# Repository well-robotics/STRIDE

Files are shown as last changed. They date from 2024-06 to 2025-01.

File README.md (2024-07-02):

# Open-Source Planar Biped Robot STRIDE
Hardware STRIDE
Simulated STRIDE
## Introduction
STRIDE is a low cost, easy-to-build yet versatile and robust planar bipedal robot platform for both educational and research purposes. The robot walks in a circular path constrained by a boom with a four-bar linkage. Except the basic robot and boom designs, a modular rough terrain setup and a quatitative measurable disturbance injection system are presented for system and algorithms validation purposes. The terrain setup can be easily reconfigured to fulfill different research purposes while the disturbance injection system built with propellors provide measurable yet decoupled disturbances to test adaptation algorithms.  
This repo includes the software and hardware design of a open-sourced planar biped robot STRIDE and a step-to-step guid on how to make mechanical assemblies and how to implement a walking controller.
## Repository Structure
The package mainly consists of two folders, one for mechanical designs and one for software. The BOM includes all the materials needed to build the robot, along with an estimated cost for each item.
## Installation
### ROS2 
This project uses ROS2 as communication middleware. To configure ROS2 on workstation or PC, we recommend using Ubuntu 22.04 and ROS2 Humble which is validated by us. \
The installation guideline of ROS2 Humble is in: https://docs.ros.org/en/humble/Installation/Ubuntu-Install-Debians.html. To configure ROS2 on Raspberry Pi 4b+, you should build from source, follow the guidelines in https://docs.ros.org/en/humble/How-To-Guides/Installing-on-Raspberry-Pi.html and https://docs.ros.org/en/humble/Installation/Alternatives/Ubuntu-Development-Setup.html. \
After installation, you can verify the setup by checking environment variables: 
```bash
  printenv | grep -i ROS
```
Once ROS2 is setup successsfully, you should first build a ROS2 workspace
```bash
mkdir -p ~/ros2_ws/src
cd ~/ros2_ws
colcon build
```
Then clone the folder
```bash
git clone https://github.com/well-robotics/STRIDE.git
```
### LibSerial
This project uses LibSerial as the serial communication middleware, the detailed installation can be found in the Github page of LibSerial: https://github.com/crayzeewulf/libserial. Following the guideline of CMake based installations and use default installation folder. 

### FROST
FROST is used to generate dynamic libraries for the project. To install FROST on Windows, follow the guidelines in https://ayonga.github.io/frost-dev/pages/installation.html. Several things should be noticed: 
1. The version of Mathematica should be equal or lower than 12.3
2. Remember to change the Mathematica version in mathrun.m
### qpOASES
qpOASES is used to solve formulated QP problems when solving for desired joint torques. To install qpOASES on Windows, follow https://github.com/coin-or/qpOASES for guidelines. Several things should be noticed: 
1. The Matlab interface should be recompiled using Visual Studio 

## Launch Example
Once all the dependencies are well configured, first build the whole package: 
```bash
cd ~/ros2_ws
colcon build
```
Then, you can run the commands below to launch simulation and hardware nodes
### MuJoco Simulation
To run the MuJoco simulation, run
```bash
ros2 launch mujoco simulation_launch.py
```
Then a MuJoco simulation window will show up and the robot will be hang in the air initially. 
### Hardware Nodes
To run hardware nodes, run 
```bash
ros2 launch hardware hardware_launch.py
```
This launch file will successfully launch all the nodes when the Arduino Mega, two IMUs and two contact switches are connected to the Raspberry Pi.

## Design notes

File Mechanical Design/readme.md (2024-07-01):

# Mechanical Design
This folder contains the mechanical design of the platform. The structure of the folder is as follow: 
1. **bipedal robot**: this folder contains the mechanical design of the robot
2. **boom**: this folder contains the mechanical design of the base and the boom
3. **hardware**: this folder contains the screws and nuts used during design
4. **rough terrain**: this folder contains the design of the modular rough terrain
A mechanical assembly video file is provided for step-to-step guideline on how to assemble the robot.

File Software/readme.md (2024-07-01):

# Software
This folder organizes the scripts used for the robot platform, categorized based on the tools they leverage.
1. **ROS2**: The ROS2 folder contains all ROS2-related scripts used for both on the hardware and the MuJoco simulator.
2. **Arduino**: The Arduino folder contains the Arduino scripts for controlling the brushed DC motors of the robot's joints and the brushless DC motors in the disturbance injection system.
3. **Matlab**: The Matlab folder contains the Matlab scripts used for generating dynamic libraries, a separate S2S dynamics based controller with QP based WBC controller and an event based simulator.

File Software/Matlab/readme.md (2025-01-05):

This folder contains the codes for dynamics library generation through FROST and a standalone implementation of a scripts based simulator, an H-LIP controller and an instantaneous QP task space controller. 

Folders are organized as follow: 
1. **Animator**: contains the animation related utilities
2. **Controller**: contains the instantaneous QP task space controller 
3. **Dynamics Gen**: contains the scripts for kinematics and dynamics functions generations
4. **Expressions**: contains the generated kinematics and dynamics functions
5. **Main Walking**: contains the utilities relevant to walking

To run the simulator and controller, simply run the script named mainWalking under Main Walking folder.

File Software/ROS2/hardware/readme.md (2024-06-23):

# hardware package
This package contains sensor reading and serial communication nodes, and the controller launch file.

## How to Use

To use this package, please use following 

To run any node, use the following command line:

```
# Check the nodes in this package (in your workspace/src folder)
source ../install/setup.bash 
ros2 pkg executables hardware

# run any node to chceck actuators or sensors:
ros2 run hardware contact_pub

# in a new command line, run this to see if the switches are functioning properlly
source ../install/setup.bash 
ros2 topic list
ros2 topic echo /hardware/ContactState
```

To launch the template controller, run the following line(make sure you have hardware setup and powered properly): 

```
ros2 launch hardware planar_bipedal_hardware_launch.py
```

## Package Structure

The following nodes are included in this package:

1. contact_sensor_node: for contact sensor reading
2. imu_node: for reading pelvis angle and angular velocity
3. roll_velocity_node: for reading x-direction velocity
4. serial_communication_joint_node: for serial communication with Arduino

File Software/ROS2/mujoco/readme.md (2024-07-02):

# Mujoco Package

This package is modified from the [open sourced ROS2 MuJoCo package](https://github.com/MindSpaceInc/Spot-MuJoCo-ROS2) from mindspace.inc.

It creates a simulation thread in MuJoCo with MJCF model file provided by description package. And established a node to send multiple sensor messages to ROS2.

## Package Structure

`MujocoMessageHandler.cpp` is the connection between MuJoCo and ROS2, it samples the required sensor data and publishes to according topics. This includes `/ContactState`, `/JointState`, `/ImuData`.(Also check communication/msg for details).

simulation executable(main.cc) establishes the physics thread in MuJoCo

## Installation Guide

This guide referenced this [installation instructions][https://gist.github.com/saratrajput/60b1310fe9d9df664f9983b38b50d5da], To download MuJoCo, please go check its [releases][https://github.com/google-deepmind/mujoco/releases]. This version of STRIDE uses [2.3.2][https://github.com/google-deepmind/mujoco/releases/tag/2.3.2]. Take 2.3.2 as an example, after downloading the zip file:

```bash
cd /home/username/
mkdir .mujoco
tar -xvf mujoco232-linux-x86_64.tar.gz -C ~/.mujoco/
```

Add these lines to your `.bashrc`:

```bas
export LD_LIBRARY_PATH=$LD_LIBRARY_PATH:/home/username/.mujoco/mujoco-2.3.2/lib
export LD_LIBRARY_PATH=$LD_LIBRARY_PATH:/usr/lib/nvidia
export PATH="$LD_LIBRARY_PATH:$PATH"
export LD_PRELOAD=/usr/lib/x86_64-linux-gnu/libGLEW.so
```

To test if the installation is successful, use the following line to test:

```bash
cd ~/.mujoco/mujoco210/bin
./simulate ../model/humanoid.xml
```

### Things to notice

1. **The hold-release procedure**: It is realized with [sim_helper](src/Planar-Bipedal-Software-Repo/mujoco/include/mujoco_sim_helper.hpp). It first holds the floating base of the robot by giving a extremely large damping and stiffness, then slowly release it to the ground.
   1. The time variables are set locally.
   2. The fixed degrees of freedom are the ones on the floating base. They will remain a small value after it is released.
2. **Applying control to MuJoCo**: check apply_ctrl() function in main.cc. It realized a PD+feedforward controller of motors in MuJoCo. The data is directly obtained from shared pointer in Message Handler Node.
3. **Launch file**: The simulation-launch file launches simulator and controller simultaneously. The model xml file and the control yaml file are also specified here.

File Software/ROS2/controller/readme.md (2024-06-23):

# Hlip package
This package implements the S2S dynamics based controller for STRIDE
## package structure
This package contains three layers of abstraction: 
1. HLIP class captures the essence of reduced-order HLIP model which plans the desired step size with reference step size
2. output_controller class is used to plan desired joint trajectories for the planar bipedal robot based on desired outputs
3. S2S_controller node takes in desired hardware inputs, instantiates a output_controller class to plan in 200Hz and outputs the desired joint positions and velocitites

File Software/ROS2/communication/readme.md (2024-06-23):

# Communication package
This package contains all the self-defined message and service interfaces being used in simulation and hardware.
## hardware interfaces  
1. ActuatorCmds.msg: for sending desired joint trajectories from Raspberry Pi to Arduino
2. ContactState.msg: for sending contact sensor states from contact sensor node to walking controller
3. JointStates.msg: for sending joint encoder readings from serial communication node to walking controller 
4. PitchState.msg: for sending pelvis angle and pelvis angular velocity to walking controller
4. MotionCommands.msg: for outputs states logging

## simulation interfaces
1. MotionCommands.msg: for outputs states logging
2. SimulationReset.srv: for MuJoco simulation reset

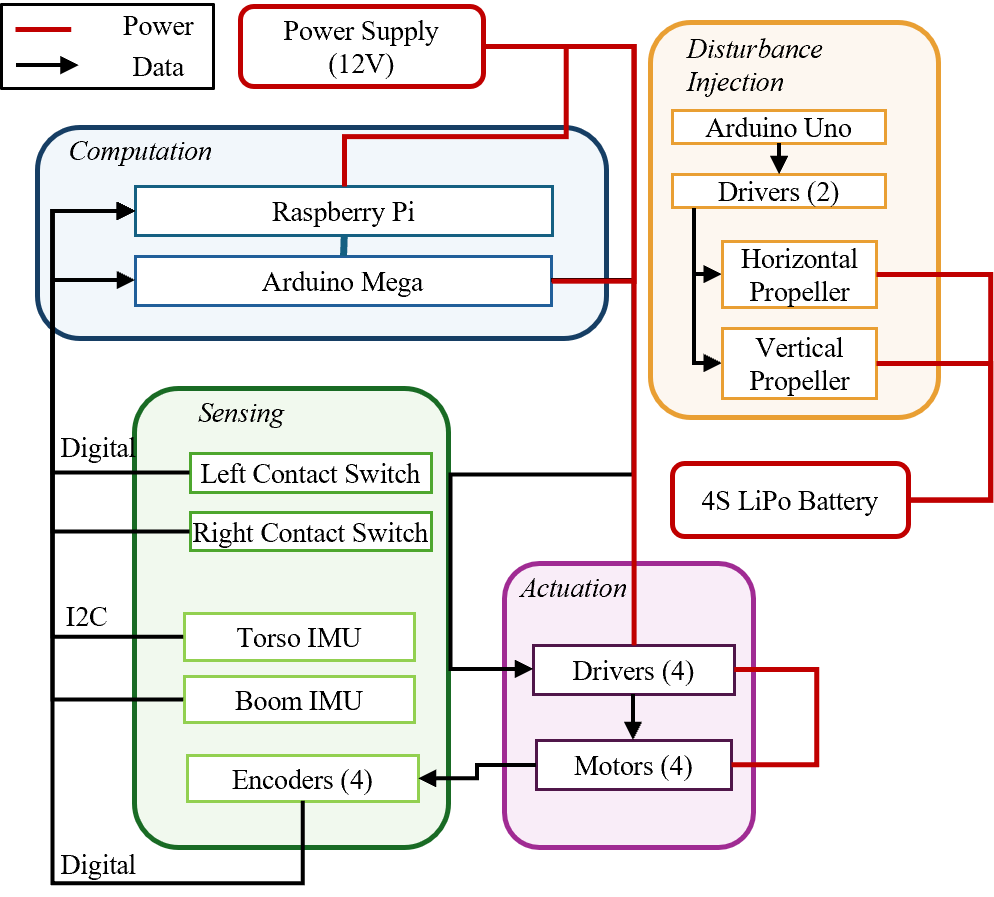
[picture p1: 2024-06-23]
electronics_diagram.png

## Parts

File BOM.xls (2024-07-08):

Mechanical parts | numbers | prices (with educational discount) | source
1140-0006-0144 | 1 | 12.74 | https://www.gobilda.com/
2800-0004-0010 | 249 | 28.8
2802-0004-0008 | 60 | 8.13
4103-0032-0312 | 1 | 7.98
1109-0024-0528 | 8 | 89.68
1139-0024-0056 | 4 | 5.94
1201-0043-0002 | 18 | 106.92
1120-0004-0120 | 3 | 17.82
1401-0043-0032 | 15 | 101.85
2800-0004-0014 | 27 | 3.14
1126-0001-0001 | 8 | 8.48
2805-0004-0108 | 16 | 8.49
2800-0004-0006 | 46 | 5.08
1204-0001-0002 | 8 | 16.96
1604-0043-0032 | 4 | 44.16
1502-0006-0020 | 4 | 1.48
1502-0006-0030 | 4 | 1.52
2803-0039-0007 | 6 | 7.62
1400-0032-0032 | 8 | 54.32
2800-0004-0012 | 12 | 3.59
4103-0032-0043 | 4 | 13.56
1506-0032-0004 | 16 | 20.32
1121-0007-0192 | 2 | 15.28
1120-0003-0096 | 2 | 10.18
1123-0043-0096 | 1 | 2.97
1201-0024-0001 | 2 | 11.88
1106-0005-0040 | 8 | 18.96
1123-0043-0144 | 2 | 7.64
1120-0001-0048 | 1 | 3.39
2800-0004-0018 | 13 | 3.31
2803-0007-0007 | 33 | 8.48
2800-0004-0030 | 4 | 3.65
1123-0043-0144 | 2 | 7.64
4103-0032-0432 | 1 | 10.02
4103-0032-0048 | 4 | 13.92
1502-0006-0010 | 2 | 1.39
2802-0004-0016 | 2 | 3.22
4103-0032-1200 | 2 | 46.06
1604-0043-0032 | 8 | 88.32
1111-0004-0001 | 2 | 11.88
1123-0043-0144 | 4 | 15.28
1116-0040-0088 | 2 | 4.74
5204-8002-0019 | 2 | 76.48
5202-2402-0019 | 2 | 76.48
1112-0001-0048 | 2 | 5.08
1611-0514-4008 | 11 | 30.54
1108-0001-0001 | 4 | 6.76
2315-1006-0030 | 2 | 25.48
1504-0032-0025 | 2 | 4.24
1108-0001-0002 | 4 | 8.48
1309-0016-4008 | 6 | 40.74
1611-0514-0006 | 2 | 3.39
1400-0032-0014 | 4 | 23.76
4100-1214-0200 | 2 | 7.64
1200-0032-0001 | 4 | 20.36
1102-0009-0072 | 4 | 5.26
1516-4008-0800 | 2 | 6.37
2315-4008-0030 | 2 | 25.48
1113-0001-0048 | 4 | 10.16
 |  |  | source: https://www.mcmaster.com/
91290A119 | 8 | 14.38
90591A121 | 8 | 1.9
98035A102 | 4 | 14.66
Electronic Parts
Arduino Uno | 1 | 17 | https://www.amazon.com/ELEGOO-Board-ATmega328P-ATMEGA16U2-Compliant/dp/B01EWOE0UU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
Arduino Mega | 1 | 20 | https://www.amazon.com/ELEGOO-Compatible-Arduino-Projects-Compliant/dp/B01H4ZLZLQ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
Raspberry Pi 4b+ | 1 | 62 | https://www.amazon.com/Raspberry-Model-2019-Quad-Bluetooth/dp/B07TC2BK1X
Pololu VNH5019 | 4 | 119.8 | https://www.pololu.com/product/1451
Gemfan Propeller 51466 | 2 | 9 | https://www.getfpv.com/gemfan-hurricane-51466-propeller-set-of-4.html
T-Motor V2207 | 2 | 27.8 | https://store.tmotor.com/product/v2207-v2-fpv-motor.html
Weight 5lb | 3 | 15 | https://www.amazon.com/Cap-2-Inch-Olympic-Weight-OPHWIS-005/dp/B09NLD1NP9?sp_csd=d2lkZ2V0TmFtZT1zcF9hdGY
SparkFun ICM20948 | 2 | 37 | https://www.sparkfun.com/products/15335
Contact Switch | 2 | 9.99 | https://www.amazon.com/gp/product/B09SLHQVHL/ref=ox_sc_saved_image_3?smid=A1POY47GM797OI&psc=1
VOYEE Xbox360 Joy Stick | 1 | 16.99 | https://www.amazon.com/VOYEE-Controller-Compatible-Microsoft-Windows/dp/B07WD4TSNQ
AC DC converter | 1 | 26.99 | https://www.amazon.com/EXENWING-12V-Universal-Converter-Transformer/dp/B0CHS2JDV8
3D printed Parts
Terrain pieces | 20 | 80.4
Footpad | 2 | 0.46
Electronics Hull | 1 | 2.2
Terrain Components
Pebble Stones |  | 25.92 | https://www.amazon.com/gp/product/B0B1T4XZRJ/ref=ox_sc_saved_image_2?smid=A1RBNAZ9ARM7RC&psc=1
Clay Pebbles |  | 15.99 | https://www.amazon.com/gp/product/B0C7CGPT5L/ref=ox_sc_saved_image_3?smid=A1NTNJ5WND4GE5&th=1
Chickpeas |  | 18.95 | https://www.amazon.com/gp/product/B001PEWJWC/ref=ox_sc_saved_image_2?smid=A74292C1GAH2Y&psc=1
Poppy Seeds |  | 5.35 | https://www.sfherb.com/Poppy-Seeds--1-Lb_p_80.html
 |  | 1775.27

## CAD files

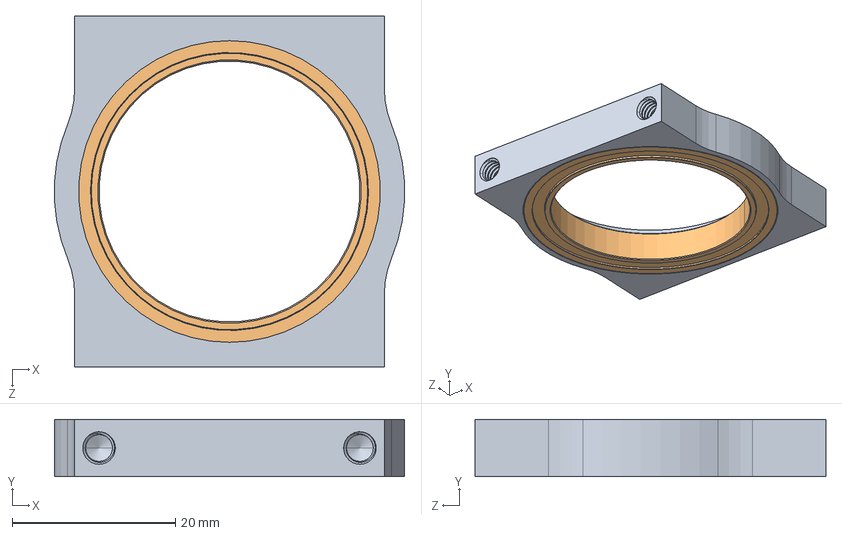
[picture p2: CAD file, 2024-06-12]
Mechanical Design/bipedal robot/robot base/1604-0043-0032 assembly.SLDASM
42.9 x 7.00 x 43.0 mm
1604-0043-0032.STEP
1601-0039-00032.STEP

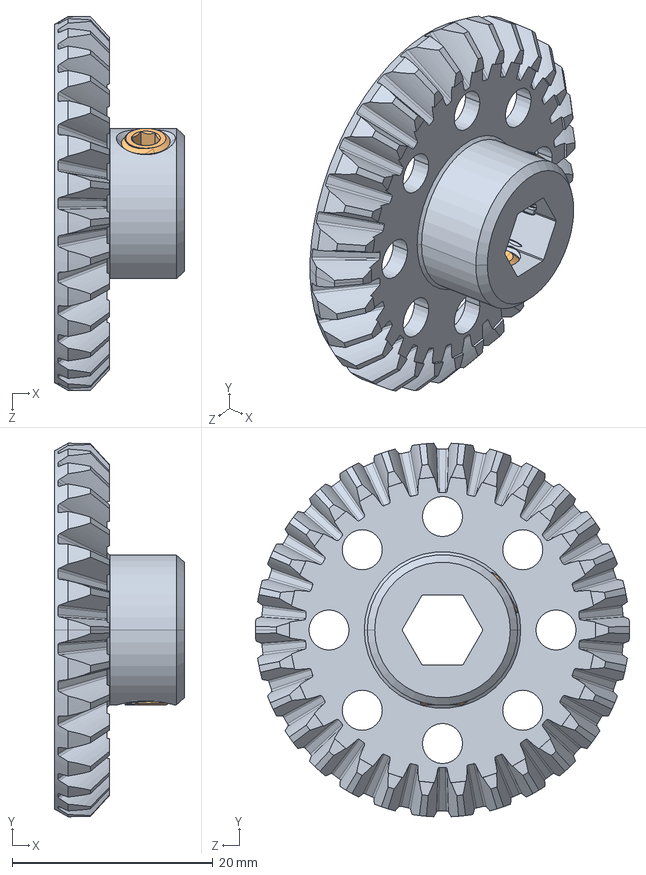
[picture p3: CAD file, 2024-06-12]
Mechanical Design/bipedal robot/robot leg knee/2315-4008-0030 assembly.SLDASM
13.0 x 37.2 x 37.3 mm
2315-4008-0030.STEP
2806-0005-0004_91390A117.STEP x 2

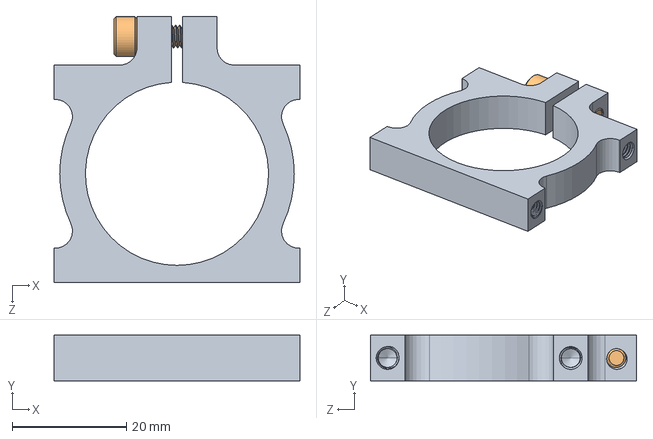
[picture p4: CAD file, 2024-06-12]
Mechanical Design/boom/bar/1401-0043-0032 assembly.SLDASM
43.0 x 8.00 x 46.5 mm
1401-0043-0032.STEP
2800-0004-0014_90128A207.STEP

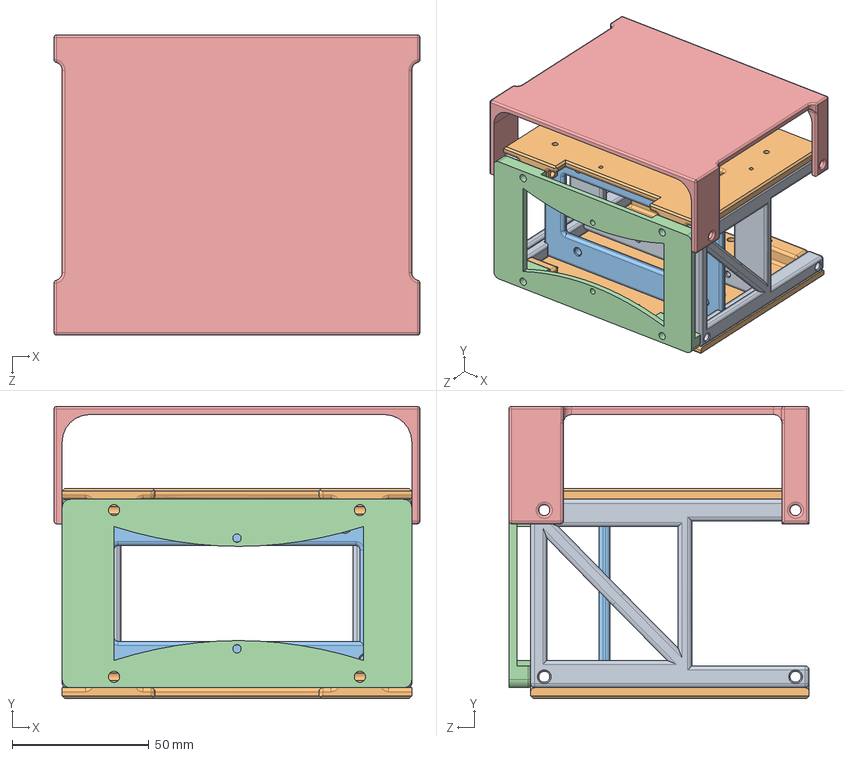
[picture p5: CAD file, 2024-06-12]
Mechanical Design/bipedal robot/Elelctronics_mounting/ElecMount.SLDASM
134.0 x 107.0 x 110.0 mm
mounting_base
shield x 2
Arduino_New
upper_energy_board
Wire_shading_part

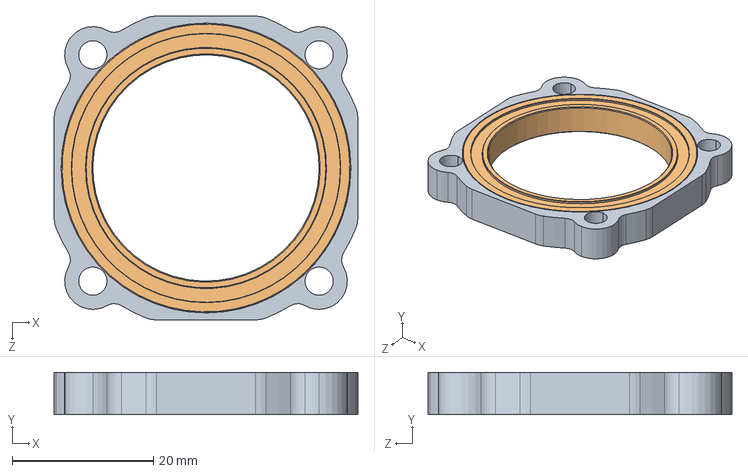
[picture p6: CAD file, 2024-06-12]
Mechanical Design/boom/bar/joint bar/1603-0032-0032 assembly.SLDASM
43.0 x 6.00 x 43.0 mm
1603-0032-0032.STEP
1601-0039-00032.STEP

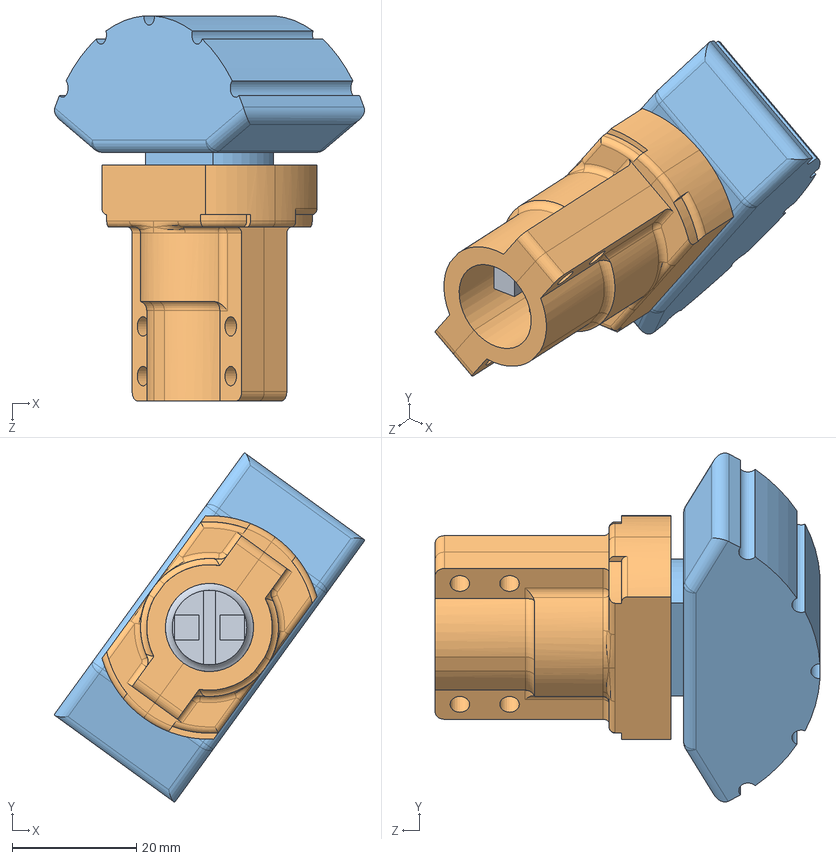
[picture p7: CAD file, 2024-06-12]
Mechanical Design/bipedal robot/contact switch/contact_TPU_footpad.SLDASM
49.9 x 56.2 x 62.0 mm
touch_sensor_bare
contact_switch_mount_half_TPU_footpad x 2
flat_foot_sticker

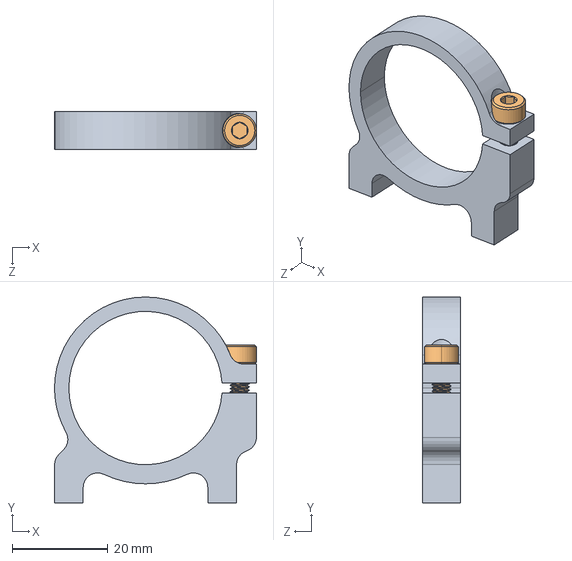
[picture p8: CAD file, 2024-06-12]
Mechanical Design/boom/base/support/1400-0032-0032 assembly.SLDASM
42.2 x 43.0 x 8.00 mm
1400-0032-0032.STEP
2800-0004-0012_90128A207.STEP

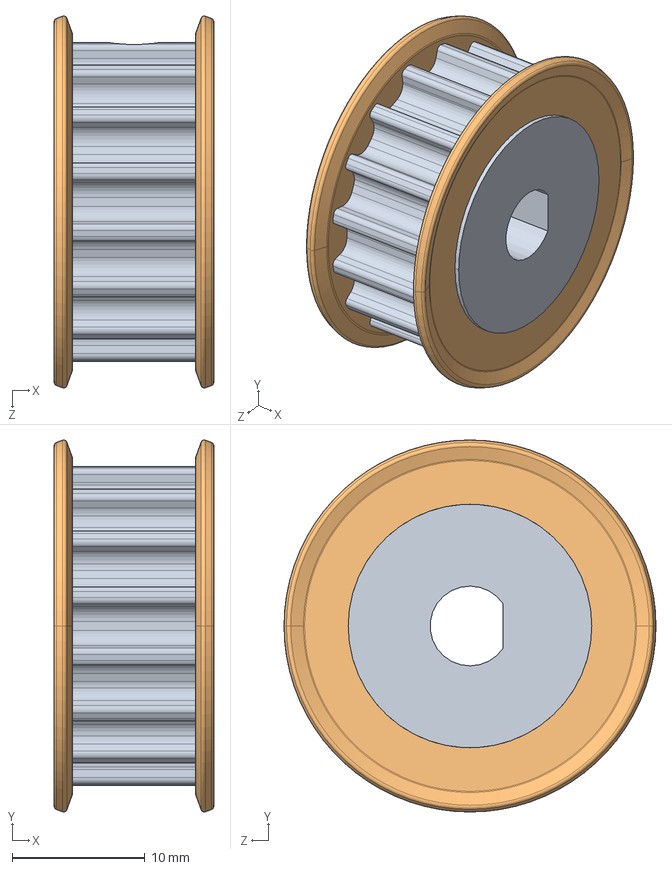
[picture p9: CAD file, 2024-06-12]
Mechanical Design/bipedal robot/3414-1006-0016 assembly.SLDASM
12.0 x 28.0 x 28.0 mm
3414-1006-0016 body.STEP
3414-4008-0016 ring.STEP x 2
2806-0005-0006_91390A118.STEP

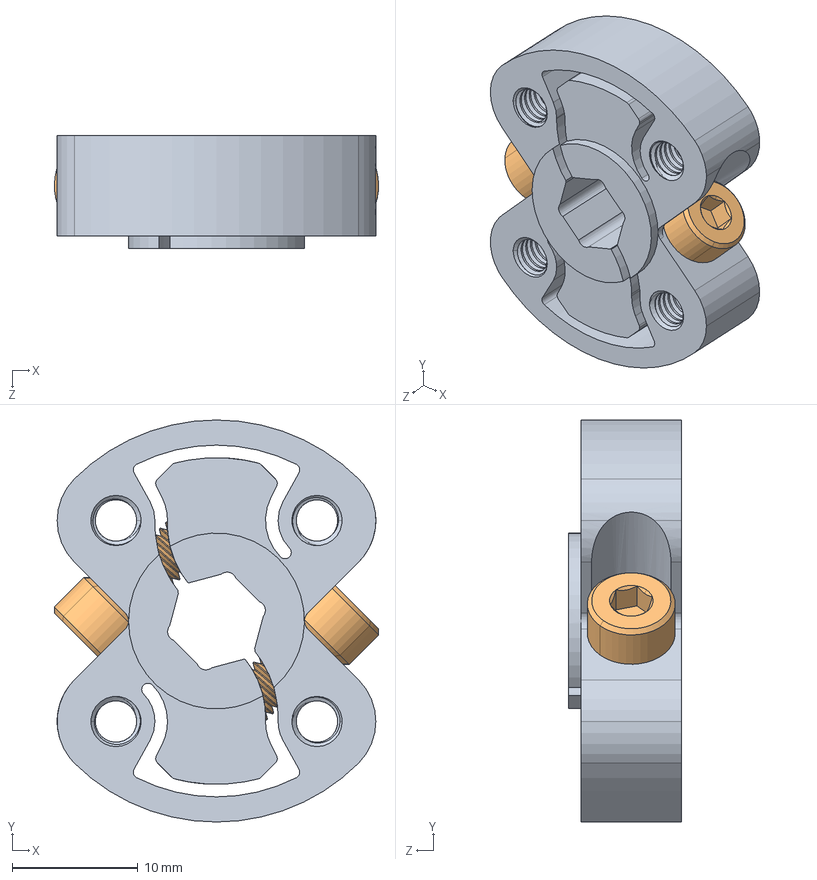
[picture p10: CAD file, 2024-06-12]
Mechanical Design/bipedal robot/robot leg knee/1309-0016-4008 assembly.SLDASM
25.8 x 32.0 x 9.00 mm
1309-0016-4008.STEP
2800-0004-0014_90128A207.STEP x 2

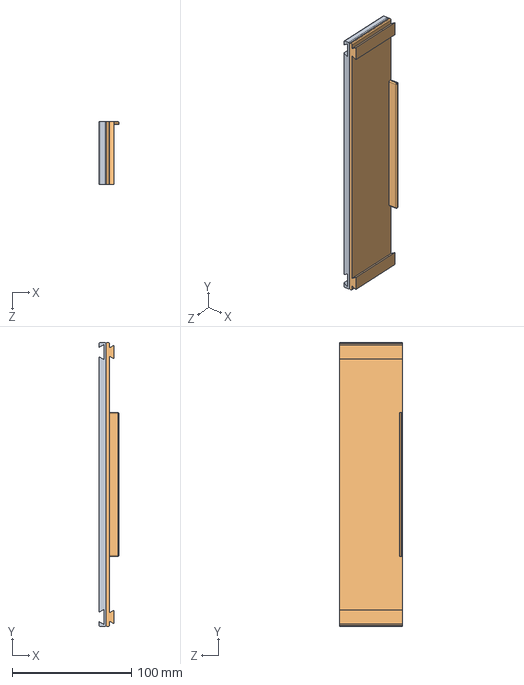
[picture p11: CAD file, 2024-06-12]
Mechanical Design/rough_terrain/middle part.SLDASM
16.8 x 238.0 x 53.0 mm
side_part_female
side_part_male

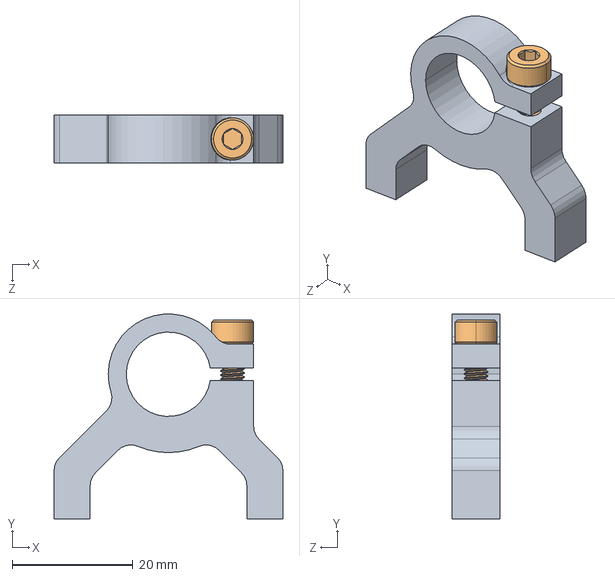
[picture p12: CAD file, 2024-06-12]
Mechanical Design/bipedal robot/robot leg knee/1400-0032-0014 assembly.SLDASM
38.0 x 34.0 x 8.00 mm
1400-0032-0014.STEP
2800-0004-0012_90128A207.STEP

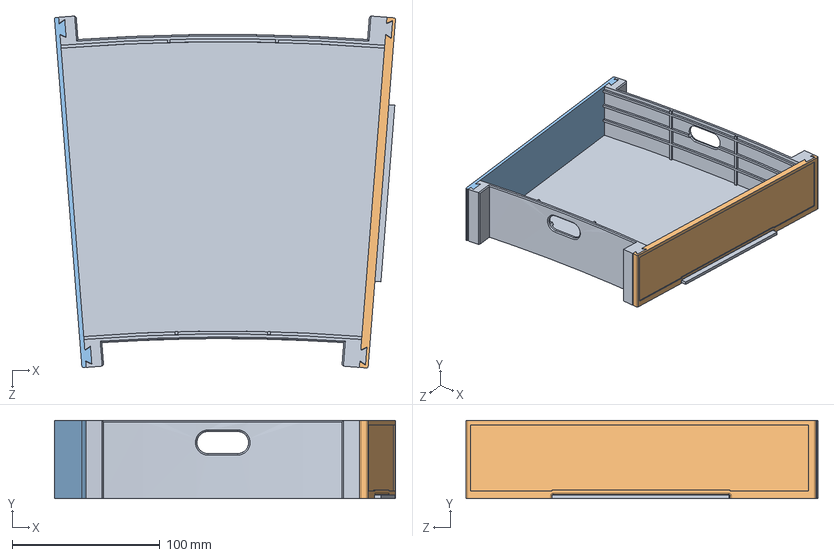
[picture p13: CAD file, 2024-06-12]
Mechanical Design/rough_terrain/side_parts_assemb.SLDASM
231.1 x 53.0 x 238.5 mm
new_terrain_piece
side_part_female
side_part_male

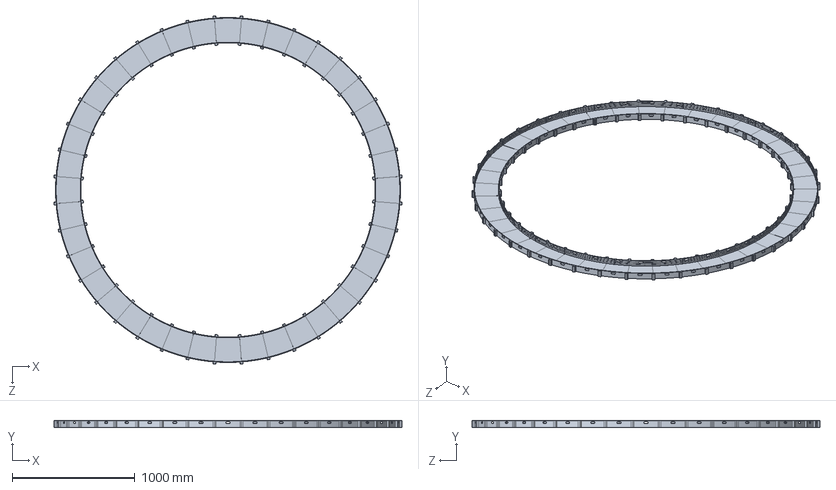
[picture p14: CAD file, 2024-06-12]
Mechanical Design/rough_terrain/terrainAssembly.SLDASM
2831.0 x 53.0 x 2831.0 mm
new_terrain_piece x 40

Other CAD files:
Mechanical Design/bipedal robot/2315-1006-0030 assembly.SLDASM
Mechanical Design/boom/bar/1604-0043-0032 assembly.SLDASM
Mechanical Design/bipedal robot/robot base/1401-0043-0032 assembly.SLDASM
Mechanical Design/boom/base/support base/1401-0043-0032 assembly.SLDASM
Mechanical Design/bipedal robot/1112-0001-0048.SLDPRT
Mechanical Design/bipedal robot/1611-0514-4008.SLDPRT
Mechanical Design/bipedal robot/3D printed parts/IMU_board.SLDPRT
Mechanical Design/bipedal robot/3D printed parts/gear_standoff_horizontal.SLDPRT
Mechanical Design/bipedal robot/3D printed parts/gear_standoff_vertical.SLDPRT
Mechanical Design/bipedal robot/Elelctronics_mounting/Arduino_New.SLDPRT
Mechanical Design/bipedal robot/Elelctronics_mounting/Wire_shading_part.SLDPRT
Mechanical Design/bipedal robot/Elelctronics_mounting/electric_mounting_cover.SLDPRT
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

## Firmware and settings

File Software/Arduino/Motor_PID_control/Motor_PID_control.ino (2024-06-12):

//// This code is about reading the encoder data using interrupts then calculate the PID values and put the PID data into the motors
#include <stdint.h> 
// serial communication variables
int motor_id[4] = {0,1,2,3}; 
const char numChars = 20;
uint8_t receiveddata[numChars];
uint8_t joint_real_encoded[8];
// double joint_states_desired[4] = {0.00,0.00,0.00,0.00};
double joint_states_desired[8] = {0.00,0.00,0.00,0.00,0.00,0.00,0.00,0.00}; 
double joint_real[4] = {0.000,0.000,0.000,0.000};

int debug_bit = 0;

// PWM pins
int PWM_pin[4] {7, 8, 11,12};  // 8 7 12 11 
int PWM_pin_cw[4] = {28,31,33,34}; 
int PWM_pin_ccw[4] = {29,30,32,35};
// PWM variables
double actual[4]; 
int direct[4] = {1,1,1,1}; 
double pwm_grav[4] = {0.0,0.0,0.0,0.0};


// Encoder pins
int encoder_pin_cw[4] = {2,18,20,21};
int encoder_pin_ccw[4] = {3,19,14,15}; 
// filter for encoders
class MovingAverageFilter{
public:  
  int window_size; 
  double previous_data[50] = {0}; // the max size of the window is set to 50
  MovingAverageFilter(int size){
    this->window_size = size; 
  } 
  double calc(){
    double output =0; 
    for(int i=0;i<window_size;i++){
      output = output + previous_data[i]; 
    }
    return (output/window_size); 
  }
  void renew(double input){
    for(int i=0;i<window_size;i++){
      previous_data[i]= previous_data[i+1]; 
    }
    previous_data[window_size - 1] = input; 
  }
};
MovingAverageFilter filter[4](2);
// encoder and position readings 
double resolution = 1992.3/(4*2*3.14159);
int count[4] = {0,0,0,0}; 
double position[4] = {0,0,0,0}; 

unsigned long start_time = millis(); 
int count_time_debug = 0; 
class PID{
public:  
  PID(double kp,double kd,double ki):Kp(kp),Kd(kd),Ki(ki){}; 
  double ComputeOutput(){
    // this function will compute the output to the PWM write function
    unsigned long now = millis(); 
    double timeChange = (double)((now - lastTime)); 
    // compute errors
    double error = this->setpoint - this->input; 
    ErrorSum += (error*timeChange); 
    double dErr = (error - lastError) / timeChange; 
    output = Kp*error + Ki*ErrorSum+ Kd*dErr;
    if (output>100){
      output = 100;
    }
    else if (output<-100){
      output = -100; 
    }
    lastError = error; 
    lastTime = now;
    return output;  
  }
  void Setsetpoint(double in){
    this-> setpoint = in;
  }
  void SetRealPosition(double pos){
    this-> input = pos; 
  }
private:   
  double Kp; 
  double Kd; 
  double Ki;  
  double ErrorSum = 0; 
  double lastError; 
  unsigned long lastTime = 0;
  double input = 0; 
  double output = 0;
  double setpoint = 0;   
};
// build up PID controllers
PID pd_controller[4]={PID(100.0,10.0,0),PID(100.0,10.0,0),PID(100.0,10.0,0),PID(100.0,10.0,0)};
void getPosition(){
  int i = 0; 
  for(i=0;i<4;i++){
    joint_real[i] = count[i]/resolution;
    filter[i].renew(joint_real[i]); 
    joint_real[i] = filter[i].calc();
  }  
}
void checkBound(){
  int i = 0;
  for(i=0;i<4;i++){
    if(i == 1 || i == 3){
    if(joint_states_desired[i] > 2.2 ){
      joint_states_desired[i] = 2.2; 
    }
    else if(joint_states_desired[i] < -1.7){
      joint_states_desired[i] = -1.7;
    }
    }
    if(i == 0 || i == 2){
    if(joint_states_desired[i] > 1.7 ){
      joint_states_desired[i] = 1.7; 
    }
    else if(joint_states_desired[i] < -1.7){
      joint_states_desired[i] = -1.7;
    }
    }

  }
}

void setup()
{
  Serial.begin(115200);
  // setup a high PWM frequency
  TCCR1A = 0b10100000;
  TCCR1B = 0b00010001;
  TCCR4A = 0b10100000;
  TCCR4B = 0b00010001;
  ICR1 = 100;
  ICR4 = 100;
  int i;
  for (i=0;i<4;i++){
    // set the encoder pin mode as input 
    pinMode(encoder_pin_cw[i],INPUT_PULLUP);
    pinMode(encoder_pin_ccw[i],INPUT_PULLUP);
    // set the PWM pin mode as output
    pinMode(PWM_pin[i],OUTPUT);
    pinMode(PWM_pin_cw[i],OUTPUT);
    pinMode(PWM_pin_ccw[i],OUTPUT);

  }
  // attach intterupt for encoder pins 
  attachInterrupt(digitalPinToInterrupt(encoder_pin_cw[0]),readEncoder<0>,RISING);
  attachInterrupt(digitalPinToInterrupt(encoder_pin_cw[1]),readEncoder<1>,RISING);
  attachInterrupt(digitalPinToInterrupt(encoder_pin_cw[2]),readEncoder<2>,RISING);
  attachInterrupt(digitalPinToInterrupt(encoder_pin_cw[3]),readEncoder<3>,RISING);
}
template<int j>
void readEncoder(){
/////////////////// method reading two pins /////////////////
  // old_val[j] = new_val[j]; 
  // new_val[j] = digitalRead(encoder_pin_cw[j])*2 + digitalRead(encoder_pin_ccw[j]);
  // out = QEM[old_val[j]*4+new_val[j]]; 
  // count[j] = count[j] + out; 

///////////////// method only read one pin  ///////////////
  int b = digitalRead(encoder_pin_ccw[j]);
  if(b>0){
    count[j]--; // ++ for pull down
  }
  else{
    count[j]++; 
  }
}

void getPosValue_byte(){
    static boolean recvInProgress = false;
    static byte ndx = 0;
    char startMarker = 's'; 
    char endMarker = 'e';
    char rc;
    while (Serial.available() > 0) { 
        rc = Serial.read();
        debug_bit = 1; 
        if (recvInProgress == true) {
            if (rc != endMarker) {
                receiveddata[ndx] = rc;
                ndx++;
                if (ndx >= numChars) {
                    ndx = numChars - 1;
                }
            }
            else {
                recvInProgress = false;
                ndx = 0;
            }
        }         
        if (rc == startMarker) {
            recvInProgress = true;
        }
    }
}

void PWMWrite(int motor_id, double DutyCycle, int direc){
  if (direc == 1){
    digitalWrite(PWM_pin_ccw[motor_id],LOW);
    digitalWrite(PWM_pin_cw[motor_id],HIGH); 
  }
  else if (direc == 0){
    digitalWrite(PWM_pin_cw[motor_id],LOW);
    digitalWrite(PWM_pin_ccw[motor_id],HIGH); 
  }
  double OutPutValue = DutyCycle*255/100;
  analogWrite(PWM_pin[motor_id],int(OutPutValue));
}

void receivedDataDecode(){
  int i;
  uint8_t j1[2];
  uint8_t j2[2];
  uint8_t j3[2];
  uint8_t j4[2];
  uint8_t j5[2];
  uint8_t j6[2];
  uint8_t j7[2];
  uint8_t j8[2];
  
  for (i = 0; i < 2; i++) {
    j1[i] = receiveddata[i];
    j2[i] = receiveddata[i + 2];
    j3[i] = receiveddata[i + 4];
    j4[i] = receiveddata[i + 6];
    j5[i] = receiveddata[i + 8];
    j6[i] = receiveddata[i + 10];
    j7[i] = receiveddata[i + 12];
    j8[i] = receiveddata[i + 14];
  }

  int16_t temp[8];
  temp[0] = (j1[0] << 8) | j1[1];
  temp[1] = (j2[0] << 8) | j2[1];
  temp[2] = (j3[0] << 8) | j3[1];
  temp[3] = (j4[0] << 8) | j4[1];
  temp[4] = (j5[0] << 8) | j5[1];
  temp[5] = (j6[0] << 8) | j6[1];
  temp[6] = (j7[0] << 8) | j7[1];
  temp[7] = (j8[0] << 8) | j8[1];

  joint_states_desired[0] = temp[0] / 100.0;
  joint_states_desired[1] = temp[1] / 100.0;
  joint_states_desired[2] = temp[2] / 100.0;
  joint_states_desired[3] = temp[3] / 100.0;
  joint_states_desired[4] = temp[4] / 100.0;
  joint_states_desired[5] = temp[5] / 100.0;
  joint_states_desired[6] = temp[6] / 100.0;
  joint_states_desired[7] = temp[7] / 100.0; 
}

void torquePWMMap(){
  // this method maps torque compensation values to PWM values using: v_pwm = R/(KT*N)*tau
  // motor params: N = 71.2, R = 1.3043, KT = 0.014
  double temp[4] = {0.0,0.0,0.0,0.0};
  int i; 
  for(i=0;i<4;i++){
    temp[i] = 1.3043/(0.014*71.2)*joint_states_desired[i+4];
    pwm_grav[i] = map(temp[i],-12.0,12.0,-100.0,100.0); 
  }
}

void sendingDataEncode() {
  // this method encode the subscribed data from double to char
  int i;
  int16_t temp[4];
  for (i = 0; i < 4; i++) {
    temp[i] = (int16_t)(float_round(joint_real[i]) * 100);  // round to two digits, times 100 and type cast to int8_t
  }
  for (i = 0; i < 4; i++) {
    joint_real_encoded[i * 2 + 1] = temp[i] & 0x00ff;   // get the byte in 0x0b
    joint_real_encoded[i * 2] = (temp[i] >> 8) & 0xff;  // get the byte in 0xb0
                                                           // cout<<hex<<(unsigned char)joint_desired_encoded[i*2]<<endl;
  }
}

float float_round(double var) {
  // this function rounds a floating point number to two decimal accuracies
  float value = (int)(var * 100);
  return (float)value / 100;
}

long int prev_val;
double generate_sine_wave_debug(){
  // step input
  // return 3.14; // rotate 180 degree
  
  // sine wave
  double period = 0.01;
  unsigned long t = millis();  
  return 3*sin((t-start_time)/period*6.28318);

  // square wave
  // if(t-start_time > 1000){
  //   if(prev_val == 0){
  //     prev_val = 3;
  //     return 3;
  //   }
  //   else{
  //     prev_val = 0;
  //     return 0;
  //   }
  //   start_time = t; 
  // }

}

void loop(){  
  // generate a sine wave for testing
  //double trajectory_debug = generate_sine_wave_debug(); 

  // read desired trajectory from Raspberry Pi 
  getPosValue_byte(); 
  receivedDataDecode();
  debug_bit == 0;
  getPosition(); 
  // send the real joint values
  sendingDataEncode();
  int i;
  Serial.write('s');
  for(i=0;i<8;i++){
    Serial.write(joint_real_encoded[i]);
  }
  Serial.write('e');

  // do PD control for motors 
  checkBound();
  for(i=0;i<4;i++){
    pd_controller[i].Setsetpoint(joint_states_desired[i]); 
    pd_controller[i].SetRealPosition(joint_real[i]);
    torquePWMMap();
    double PWM = pd_controller[i].ComputeOutput()+pwm_grav[i]; 
    if(PWM < 0){
      PWM = -PWM; 
      direct[i] = 0; 
    }
    else{
      direct[i] = 1; 
    }
    PWMWrite(i,PWM,direct[i]); 
 }
  long int b = micros();
}

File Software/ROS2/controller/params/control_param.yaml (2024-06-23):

# sim_controller:
#   ros__parameters:
#     # kp_hip:  2.   #4. #1.6 #0.8
#     # kp_knee: 1.   #2.5 #1.2 #0.4
#     # kd_hip:  .4   #2.5 #.2
#     # kd_knee: .2  #0.2 #0.12
#     kp_hip:  30.  #25.   #4. #1.6 #0.8
#     kp_knee: 30. #25.   #2.5 #1.2 #0.4
#     kd_hip:  0.2 #0.5   #2.5 #.2
#     kd_knee: 0.2 #0.5 #0.2 #0.12
#     pelvis_init_height: 0.450
#     swing_height: 0.06
#     TSSP: 0.4 # 0.35
#     step_size: 0.1 # 0.2
#     vdes: 0.25
#     COM_height: 0.30 # 0.35

#     com_height_test: 0.30
#     x_swing_test: 0.
#     z_swing_test: 0.0
#     pitch_test: 0.

# tuned using straight knee and straight footpad, Mar 22
S2S_controller:
  ros__parameters:
    kp_hip:  15.
    kp_knee: 15.
    kd_hip:  0.1
    kd_knee: 0.1
    pelvis_init_height: 0.5
    swing_height: 0.06
    TSSP: 0.4
    step_size: 0.08
    vdes: 0.0
    COM_height: 0.34
    # com_height_test: 0.33
    x_swing_test: 0.
    z_swing_test: 0.0
    pitch_test: 0.

sim_hard_bridge:
  ros__parameters:
    kp_hip:  40.
    kp_knee: 40.
    kd_hip:  1.0 #0.6
    kd_knee: 0.6 #0.6
#### before adding gear ratio
    # kp_hip:  50.  
    # kp_knee: 50. 
    # kd_hip:  1. #0.6
    # kd_knee: 1. #0.6

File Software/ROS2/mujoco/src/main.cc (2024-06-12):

//  ros2_mujoco,
// WELL-robotics
// Xiaobin Xiong, modified based on mujoco example and deepbreak example.

#include <chrono>
#include <cstdint>
#include <cstdio>
#include <cstring>
#include <iostream>
#include <memory>
#include <mutex>
#include <new>
#include <string>
#include <thread>
#include <type_traits>
#include <vector>

#include "array_safety.h"
#include "glfw_adapter.h"
#include "simulate.h"
#include <mujoco/mujoco.h>

#include "mujoco_sim_helper.hpp"
#include "MuJoCoMessageHandler.h"
// #include "ros_utilities/ros_utilities.hpp"

#define MUJOCO_PLUGIN_DIR "mujoco_plugin"

extern "C"
{
#include <sys/errno.h>
#include <unistd.h>
}

namespace
{
  namespace mj = ::mujoco;
  namespace mju = ::mujoco::sample_util;

  // constants
  const double syncMisalign =
      0.1; // maximum mis-alignment before re-sync (simulation seconds)
  const double simRefreshFraction =
      0.7;                       // fraction of refresh available for simulation
  const int kErrorLength = 1024; // load error string length

  // model and data
  mjModel *m = nullptr;
  mjData *d = nullptr;

  // control noise variables
  mjtNum *ctrlnoise = nullptr;
  std::shared_ptr<mujoco_ros2::MuJoCoMessageHandler::ActuatorCmds> actuator_cmds_ptr;

  using Seconds = std::chrono::duration<double>;

  //---------------------------------------- plugin handling
  //-----------------------------------------

  // return the path to the directory containing the current executable
  // used to determine the location of auto-loaded plugin libraries
  std::string getExecutableDir()
  {

    constexpr char kPathSep = '/';
    const char *path = "/proc/self/exe";
    std::string realpath = [&]() -> std::string
    {
      std::unique_ptr<char[]> realpath(nullptr);
      std::uint32_t buf_size = 128;
      bool success = false;
      while (!success)
      {
        realpath.reset(new (std::nothrow) char[buf_size]);
        if (!realpath)
        {
          std::cerr << "cannot allocate memory to store executable path\n";
          return "";
        }

        std::size_t written = readlink(path, realpath.get(), buf_size);
        if (written < buf_size)
        {
          realpath.get()[written] = '\0';
          success = true;
        }
        else if (written == -1)
        {
          if (errno == EINVAL)
          {
            // path is already not a symlink, just use it
            return path;
          }

          std::cerr << "error while resolving executable path: "
                    << strerror(errno) << '\n';
          return "";
        }
        else
        {
          // realpath is too small, grow and retry
          buf_size *= 2;
        }
      }
      return realpath.get();
    }();

    if (realpath.empty())
    {
      return "";
    }

    for (std::size_t i = realpath.size() - 1; i > 0; --i)
    {
      if (realpath.c_str()[i] == kPathSep)
      {
        return realpath.substr(0, i);
      }
    }

    // don't scan through the entire file system's root
    return "";
  }

  // scan for libraries in the plugin directory to load additional plugins
  void scanPluginLibraries()
  {
    // check and print plugins that are linked directly into the executable
    int nplugin = mjp_pluginCount();
    if (nplugin)
    {
      std::printf("Built-in plugins:\n");
      for (int i = 0; i < nplugin; ++i)
      {
        std::printf("    %s\n", mjp_getPluginAtSlot(i)->name);
      }
    }
    const std::string sep = "/";
    // try to open the ${EXECDIR}/plugin directory
    // ${EXECDIR} is the directory containing the simulate binary itself
    const std::string executable_dir = getExecutableDir();
    
   
    if (executable_dir.empty())
    {
      return;
    }
    const std::string plugin_dir = getExecutableDir() + sep + MUJOCO_PLUGIN_DIR;
    mj_loadAllPluginLibraries(
        plugin_dir.c_str(), +[](const char *filename, int first, int count)
                            {
        std::printf("Plugins registered by library '%s':\n", filename);
        for (int i = first; i < first + count; ++i) {
          std::printf("    %s\n", mjp_getPluginAtSlot(i)->name);
        } });
  }

  //------------------------------------------- simulation
  //-------------------------------------------

  mjModel *LoadModel(const char *file, mj::Simulate &sim)
  {
    // this copy is needed so that the mju::strlen call below compiles
    char filename[mj::Simulate::kMaxFilenameLength];
    mju::strcpy_arr(filename, file);

    RCLCPP_INFO(rclcpp::get_logger("MuJoCo"), "load model from: %s\n", filename);

    // make sure filename is not empty
    if (!filename[0])
    {
      return nullptr;
    }

    // load and compile
    char loadError[kErrorLength] = "";
    mjModel *mnew = 0;
    if (mju::strlen_arr(filename) > 4 &&
        !std::strncmp(filename + mju::strlen_arr(filename) - 4, ".mjb",
                      mju::sizeof_arr(filename) - mju::strlen_arr(filename) +
                          4))
    {
      mnew = mj_loadModel(filename, nullptr);
      if (!mnew)
      {
        mju::strcpy_arr(loadError, "could not load binary model");
      }
    }
    else
    {
      mnew = mj_loadXML(filename, nullptr, loadError,
                        mj::Simulate::kMaxFilenameLength);
      // remove trailing newline character from loadError
      if (loadError[0])
      {
        int error_length = mju::strlen_arr(loadError);
        if (loadError[error_length - 1] == '\n')
        {
          loadError[error_length - 1] = '\0';
        }
      }
    }

    mju::strcpy_arr(sim.loadError, loadError);

    if (!mnew)
    {
      std::printf("%s\n", loadError);
      return nullptr;
    }

    // compiler warning: print and pause
    if (loadError[0])
    {
      // mj_forward() below will print the warning message
      std::printf("Model compiled, but simulation warning (paused):\n  %s\n",
                  loadError);
      sim.run = 0;
    }

    return mnew;
  }

  // PD_CONTROL: to apply control to the motor in mujoco
  void apply_ctrl(mjModel *m, mjData *d)
  {
    // std::cout<< "start applying ctrl"  <<std::endl;
    for (size_t k = 0; k < actuator_cmds_ptr->actuators_name.size(); k++)
    {
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

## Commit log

2024-06-12 initial push for mechanical designs
    [1102-0009-0072.SLDPRT, 1106-0005-0040.SLDPRT, 1108-0001-0001.SLDPRT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]
2024-06-23 add the BOM
    [BOM.xls]
2024-06-23 update the readmes and clean up description folder
    [BOM.xls]
2024-06-23 change exponential moving average filter to low pass filter, delete ekf
2024-07-08 renew the BOM with educational price
    [BOM.xls]
